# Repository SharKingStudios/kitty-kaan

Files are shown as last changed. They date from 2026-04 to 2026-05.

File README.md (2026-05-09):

# kitty kaan

*Acceleration controlled cat ears for our FRC driver ;)*

## What is this?

**kitty kaan** is a wearable pair of motorized cat ears designed for our FRC driver. The ears react to acceleration, making them move with the driver in a more expressive way.

The project combines a small electronics stack and compact mounting hardware into a lightweight assembly. An accelerometer detects motion, and the control electronics translate that movement into ear movement. The result is a simple but very silly accessory that gives the driver a pair of responsive “kitty ears.”

This was designed as a small CAD and electronics integration project. A big part of the challenge was packaging everything into the smallest form factor possible while still keeping the assembly buildable. Instead of using one large controller board, the electronics were split across smaller breakout boards so they could fit into tighter spaces and be arranged more flexibly.

---

## Renders

Screenshot 2026-04-08 at 22-41-47 Kitty Kaan Main Assembly




---

## Some context

Its a simpler project for a simple idea.

The goal was to make the electronics stack as small as physically possible, which is why seperate breakouts were used. They also added to the simplicity of the design (which is nice).

Fitting everything together was the hardest part of this mini project, but it turned out looking pretty awesome!

## Journaling

This project was made for Hack Club's Stasis program!

You can check out my project journal [here](https://stasis.hackclub.com/dashboard/projects/cmni7bl1i00i401np7ca4izak)!

## Bill of Materials

| Qty | Item | URL | Unit Price (USD) | Total (USD) | Notes |
| ---: | --- | --- | ---: | ---: | --- |
| 1 | Adafruit MiniBoost 5V @ 1A - TPS61023 | [adafruit.com/product/4654](https://www.adafruit.com/product/4654) | $3.95 | $3.95 |  |
| 1 | 9g Servo Set | [Amazon](https://www.amazon.com/Control-Raspberry-Helicopter-Airplane-Controls/dp/B0DFL7QZRJ) | $6.99 | $6.99 | For 4× 9g servos |
| 1 | Seeed XIAO RA4M1 | [Amazon](https://www.amazon.com/Compatible-Arduino-Renesas-Tolerant-Ultra-Compact/dp/B0DF9VJDJ7) | $9.90 | $9.90 |  |
| 1 | JST Battery Connector | — | $0.00 | $0.00 | Whatever matches your battery |
| 1 | Some Battery | — | $0.00 | $0.00 | Pick your favorite |
| 1 | MPU-6050 IMU | [Amazon](https://www.amazon.com/HiLetgo-MPU-6050-Accelerometer-Gyroscope-Converter/dp/B01DK83ZYQ) | $6.99 | $6.99 |  |
| 1 | PCB + Shipping | JLCPCB | $15.00 | $15.00 |  |
|  | **Total** |  |  | **$42.83** |  |

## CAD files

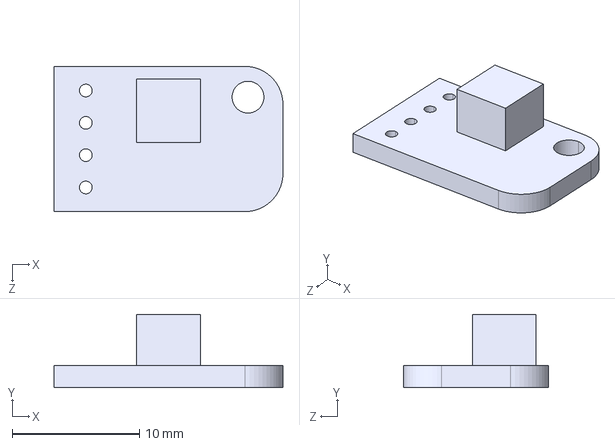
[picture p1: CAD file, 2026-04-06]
PCB/Custom Parts/Adafruit TPS61023.STEP
18.0 x 5.75 x 11.4 mm

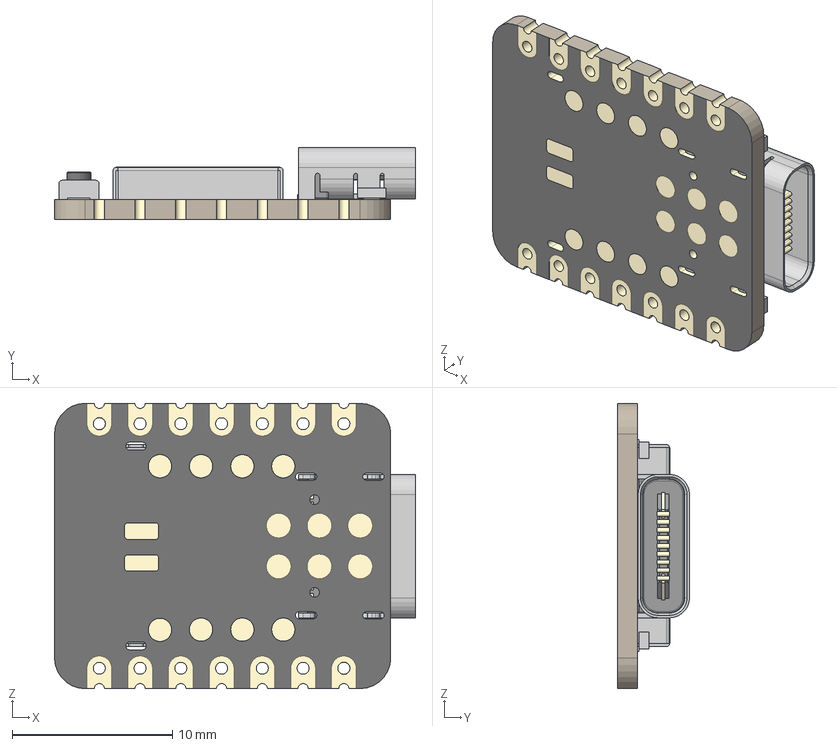
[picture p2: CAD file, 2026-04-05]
PCB/Custom Parts/Seeed Studio XIAO RA4M1 v3.step
22.5 x 4.49 x 17.8 mm
BOSS-EXTRUDE14_8_
BOSS-EXTRUDE7_4_
BOSS-EXTRUDE7_3_
BOSS-EXTRUDE14_4_
BOSS-EXTRUDE14_2_
BOSS-EXTRUDE14_11_
BOSS-EXTRUDE7_7_
BOSS-EXTRUDE14_9_
BOSS-EXTRUDE14_3_
BOSS-EXTRUDE14_7_
MIRROR2
BOSS-EXTRUDE14_5_
BOSS-EXTRUDE14_12_
BOSS-EXTRUDE7_8_
BOSS-EXTRUDE7_1_
BOSS-EXTRUDE14_10_
BOSS-EXTRUDE7_9_
BOSS-EXTRUDE14_6_
BOSS-EXTRUDE14_1_
BOSS-EXTRUDE7_6_
BOSS-EXTRUDE7_2_
CUT-EXTRUDE5
BOSS-EXTRUDE7_5_
Button (1) x 2
Shield

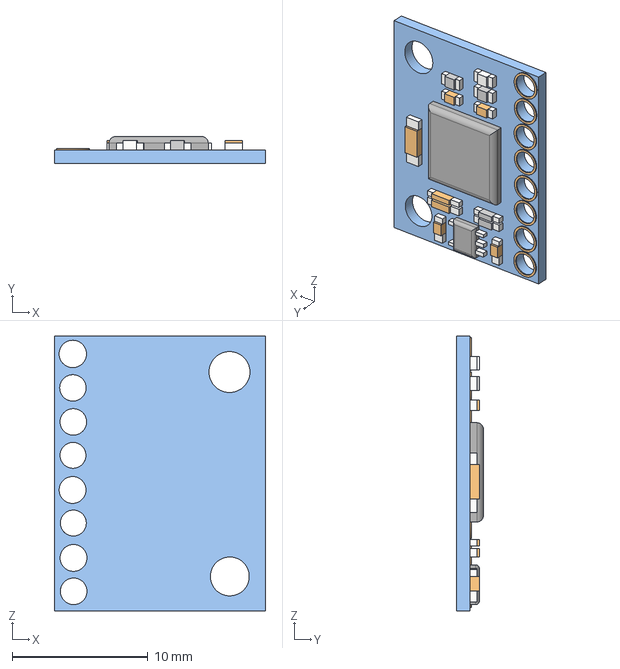
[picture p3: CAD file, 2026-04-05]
PCB/Custom Parts/MPU6050 v2.step
15.6 x 2.00 x 20.3 mm

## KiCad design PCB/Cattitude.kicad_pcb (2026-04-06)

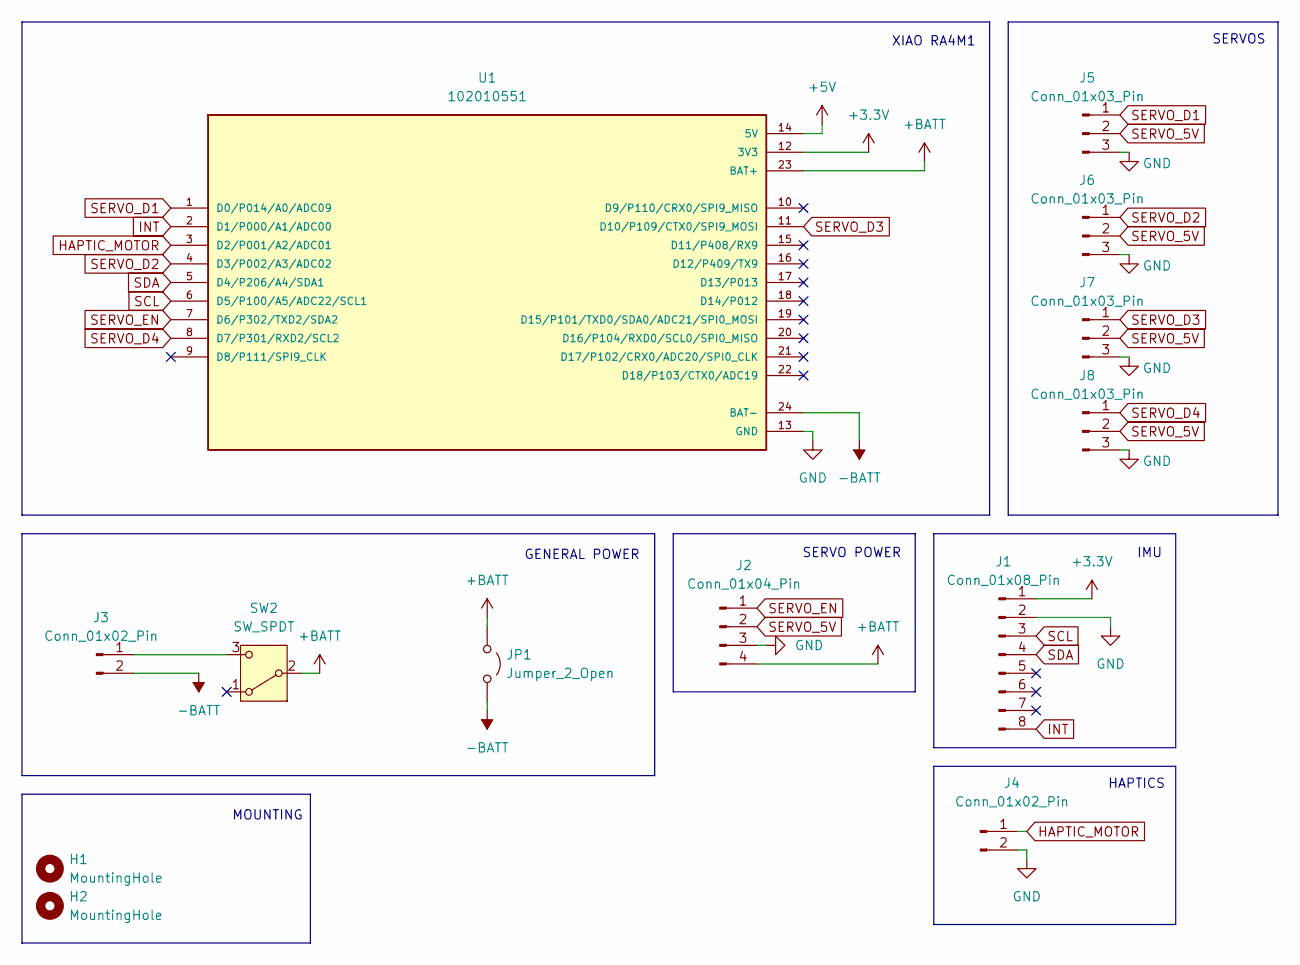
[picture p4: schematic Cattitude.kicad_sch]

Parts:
H1, H2: MountingHole; MountingHole_2.7mm_M2.5_DIN965_Pad
J1: Conn_01x08_Pin; MPU 6050
J2: Conn_01x04_Pin; PinHeader_1x04_P2.54mm_Vertical
J3: Conn_01x02_Pin; JST_EH_B2B-EH-A_1x02_P2.50mm_Vertical
J4: Conn_01x02_Pin; PinHeader_1x02_P2.54mm_Vertical
J5, J6, J7, J8: Conn_01x03_Pin; PinHeader_1x03_P2.54mm_Horizontal
JP1: Jumper_2_Open; TestPoint_2Pads_Pitch2.54mm_Drill0.8mm
SW2: SW_SPDT; SW_Slide_SPDT_Angled_CK_OS102011MA1Q
U1: 102010551; XIAO RA4M1; PARTREV NA

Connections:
+3.3V: J1.1, U1.12 (3V3)
+5V: U1.14 (5V)
+BATT: J2.4, JP1.1 (A), SW2.2 (B), U1.23 (BAT+)
-BATT: J3.2, JP1.2 (B), U1.24 (BAT-)
GND: J1.2, J2.3, J4.2, J5.3, J6.3, J7.3, J8.3, U1.13 (GND)
HAPTIC_MOTOR: J4.1, U1.3 (D2/P001/A2/ADC01)
INT: J1.8, U1.2 (D1/P000/A1/ADC00)
unnamed: J3.1, SW2.3 (C)
SCL: J1.3, U1.6 (D5/P100/A5/ADC22/SCL1)
SDA: J1.4, U1.5 (D4/P206/A4/SDA1)
SERVO_5V: J2.2, J5.2, J6.2, J7.2, J8.2
SERVO_D1: J5.1, U1.1 (D0/P014/A0/ADC09)
SERVO_D2: J6.1, U1.4 (D3/P002/A3/ADC02)
SERVO_D3: J7.1, U1.11 (D10/P109/CTX0/SPI9_MOSI)
SERVO_D4: J8.1, U1.8 (D7/P301/RXD2/SCL2)
SERVO_EN: J2.1, U1.7 (D6/P302/TXD2/SDA2)

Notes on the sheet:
SERVOS
MOUNTING
HAPTICS
XIAO RA4M1
SERVO POWER
GENERAL POWER
IMU

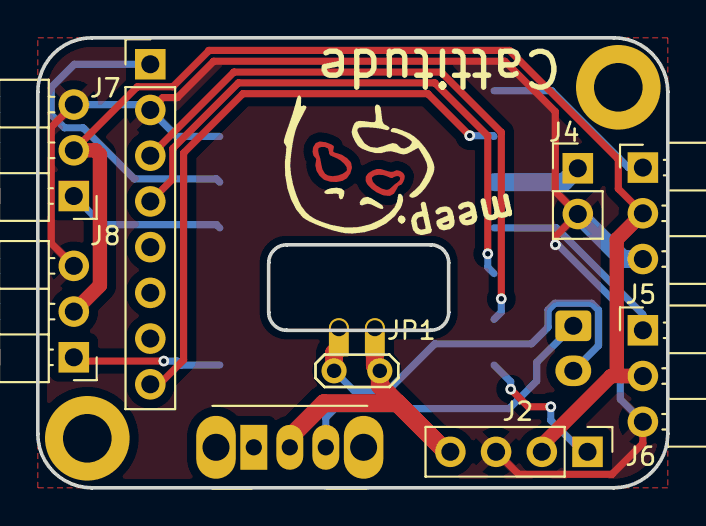
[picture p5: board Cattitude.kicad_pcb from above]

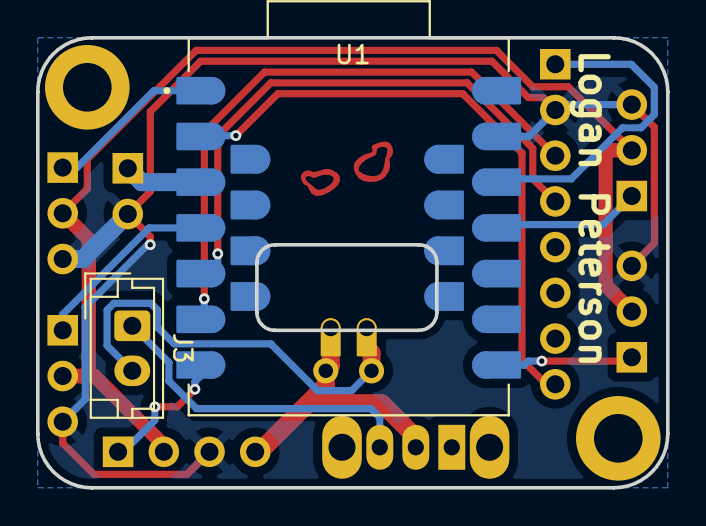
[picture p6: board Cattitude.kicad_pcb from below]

Board: 2 copper layers, 35.0 x 25.0 mm, 13 parts (2 on the bottom side), 15 nets.

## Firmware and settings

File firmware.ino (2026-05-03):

/*
  Kitty Kaan Cat Ear Firmware
  Board: Seeed XIAO RA4M1
  IMU: MPU6050/GY-521 style module
  Servos: 4 expressive cat-ear servos

  Schematic pin mapping:
    SERVO_D1  -> D0
    IMU_INT   -> D1
    HAPTIC    -> D2, unused here
    SERVO_D2  -> D3
    SDA       -> D4
    SCL       -> D5
    SERVO_EN  -> D6
    SERVO_D4  -> D7
    SERVO_D3  -> D10
*/

#include <Wire.h>
#include <Servo.h>
#include <Adafruit_MPU6050.h>
#include <Adafruit_Sensor.h>

#if defined(ARDUINO_ARCH_RENESAS)
  #include <Arduino.h>
#endif

// -------------------- Pins --------------------

const int PIN_SERVO_1 = D0;
const int PIN_IMU_INT = D1;
const int PIN_HAPTIC  = D2;
const int PIN_SERVO_2 = D3;
const int PIN_SERVO_EN = D6;
const int PIN_SERVO_4 = D7;
const int PIN_SERVO_3 = D10;

const int PIN_STATUS_LED = LED_BUILTIN;

// Battery ADC pin.
// If your XIAO core exposes PIN_VBAT or BATTERY_PIN, this will use it.
// If not, battery monitoring will safely default to 100%.
#if defined(PIN_VBAT)
const int PIN_BATTERY_ADC = PIN_VBAT;
#elif defined(BATTERY_PIN)
const int PIN_BATTERY_ADC = BATTERY_PIN;
#elif defined(VBAT_ENABLE)
const int PIN_BATTERY_ADC = VBAT_ENABLE;
#else
const int PIN_BATTERY_ADC = -1;
#endif

// -------------------- Hardware --------------------

Adafruit_MPU6050 mpu;

Servo servo1;
Servo servo2;
Servo servo3;
Servo servo4;

volatile bool imuInterruptSeen = false;

// -------------------- Tuning --------------------

// Servo center positions.
// Adjust these if your mechanical center is not exactly 90.
int center1 = 90;
int center2 = 90;
int center3 = 90;
int center4 = 90;

// Servo travel limits.
const int SERVO_MIN = 35;
const int SERVO_MAX = 145;

// Overall expressiveness.
const float PITCH_GAIN = 0.95f;
const float ROLL_GAIN  = 0.80f;
const float SWAY_GAIN  = 1.15f;

// Smoothness.
// Higher = smoother/slower.
const float SERVO_SMOOTHING = 0.13f;

// Movement thresholds.
const float ACTIVE_ACCEL_DELTA_G = 0.065f;
const float ACTIVE_GYRO_DPS      = 4.0f;

// Sleep after this much stillness.
const unsigned long SLEEP_AFTER_MS = 90000UL;

// Low battery cutoff.
const float LOW_BATTERY_PERCENT = 20.0f;

// LiPo voltage range.
const float LIPO_EMPTY_V = 3.30f;
const float LIPO_FULL_V  = 4.20f;

// If your battery ADC reads through a divider, set this.
// Example: 2.0 if ADC sees half the battery voltage.
// For built-in VBAT sensing this is often already handled by the core,
// but leave this here for easy adjustment.
const float BATTERY_DIVIDER_RATIO = 1.0f;

// XIAO / Arduino ADC reference assumption.
// Adjust only if your board core reports a different ADC scale.
const float ADC_REFERENCE_V = 3.3f;
const int ADC_MAX_COUNTS = 4095;

// Servo update rate.
const unsigned long SERVO_UPDATE_MS = 20;

// -------------------- State --------------------

float servoPos1 = 90;
float servoPos2 = 90;
float servoPos3 = 90;
float servoPos4 = 90;

float sway = 0.0f;
float swayVelocity = 0.0f;

unsigned long lastMotionMs = 0;
unsigned long lastServoUpdateMs = 0;
unsigned long lastBatteryCheckMs = 0;
unsigned long lastLowBatteryBlinkMs = 0;

float batteryPercent = 100.0f;
bool lowBattery = false;
bool servosEnabled = false;

// -------------------- Helpers --------------------

void imuISR() {
  imuInterruptSeen = true;
}

int clampServo(int v) {
  if (v < SERVO_MIN) return SERVO_MIN;
  if (v > SERVO_MAX) return SERVO_MAX;
  return v;
}

float clampFloat(float v, float lo, float hi) {
  if (v < lo) return lo;
  if (v > hi) return hi;
  return v;
}

float lipoVoltageToPercent(float v) {
  // Simple single-cell LiPo percentage curve.
  // This is intentionally conservative around the lower end.
  if (v >= 4.20f) return 100.0f;
  if (v <= 3.30f) return 0.0f;

  if (v >= 4.10f) return 90.0f + (v - 4.10f) * 100.0f;
  if (v >= 4.00f) return 75.0f + (v - 4.00f) * 150.0f;
  if (v >= 3.90f) return 55.0f + (v - 3.90f) * 200.0f;
  if (v >= 3.80f) return 35.0f + (v - 3.80f) * 200.0f;
  if (v >= 3.70f) return 20.0f + (v - 3.70f) * 150.0f;
  if (v >= 3.60f) return 10.0f + (v - 3.60f) * 100.0f;
  return (v - 3.30f) * 33.33f;
}

float readBatteryVoltage() {
  if (PIN_BATTERY_ADC < 0) {
    return 4.20f;
  }

  analogReadResolution(12);

  const int samples = 16;
  long total = 0;

  for (int i = 0; i < samples; i++) {
    total += analogRead(PIN_BATTERY_ADC);
    delay(2);
  }

  float raw = total / float(samples);
  float measured = (raw / ADC_MAX_COUNTS) * ADC_REFERENCE_V;
  return measured * BATTERY_DIVIDER_RATIO;
}

void updateBatteryStatus() {
  unsigned long now = millis();

  if (now - lastBatteryCheckMs < 5000UL) {
    return;
  }

  lastBatteryCheckMs = now;

  float vbat = readBatteryVoltage();
  batteryPercent = lipoVoltageToPercent(vbat);
  lowBattery = batteryPercent < LOW_BATTERY_PERCENT;
}

void enableServos() {
  if (servosEnabled) return;

  digitalWrite(PIN_SERVO_EN, HIGH);
  delay(100);

  servo1.attach(PIN_SERVO_1);
  servo2.attach(PIN_SERVO_2);
  servo3.attach(PIN_SERVO_3);
  servo4.attach(PIN_SERVO_4);

  servosEnabled = true;
}

void disableServos() {
  if (!servosEnabled) return;

  servo1.detach();
  servo2.detach();
  servo3.detach();
  servo4.detach();

  delay(20);
  digitalWrite(PIN_SERVO_EN, LOW);

  servosEnabled = false;
}

void writeServoSmooth(Servo &s, float &current, int target) {
  current += (target - current) * SERVO_SMOOTHING;
  s.write(clampServo((int)(current + 0.5f)));
}

void centerEarsAndStop() {
  enableServos();

  for (int i = 0; i < 60; i++) {
    writeServoSmooth(servo1, servoPos1, center1);
    writeServoSmooth(servo2, servoPos2, center2);
    writeServoSmooth(servo3, servoPos3, center3);
    writeServoSmooth(servo4, servoPos4, center4);
    delay(20);
  }

  disableServos();
}

void blinkLowBattery() {
  unsigned long now = millis();

  if (now - lastLowBatteryBlinkMs >= 500UL) {
    lastLowBatteryBlinkMs = now;
    digitalWrite(PIN_STATUS_LED, !digitalRead(PIN_STATUS_LED));
  }
}

void configureMPUMotionInterrupt() {
  // Motion interrupt is used to wake from idle/light sleep.
  // Threshold is in MPU6050 motion units, not g directly.
  mpu.setHighPassFilter(MPU6050_HIGHPASS_0_63_HZ);
  mpu.setMotionDetectionThreshold(3);
  mpu.setMotionDetectionDuration(20);
  mpu.setInterruptPinLatch(true);
  mpu.setInterruptPinPolarity(true);
  mpu.setMotionInterrupt(true);
}

void clearMPUInterrupt() {
  sensors_event_t a, g, temp;
  mpu.getEvent(&a, &g, &temp);
  imuInterruptSeen = false;
}

void enterLightSleepUntilMotion() {
  centerEarsAndStop();

  clearMPUInterrupt();
  attachInterrupt(digitalPinToInterrupt(PIN_IMU_INT), imuISR, RISING);

  digitalWrite(PIN_STATUS_LED, LOW);

  while (!imuInterruptSeen) {
    updateBatteryStatus();

    if (lowBattery) {
      blinkLowBattery();
      delay(100);
      continue;
    }

    // ARM light sleep. An external interrupt wakes execution here.
    #if defined(__arm__) || defined(ARDUINO_ARCH_RENESAS)
      __DSB();
      __WFI();
      __ISB();
    #else
      delay(250);
    #endif
  }

  detachInterrupt(digitalPinToInterrupt(PIN_IMU_INT));
  clearMPUInterrupt();

  lastMotionMs = millis();
  digitalWrite(PIN_STATUS_LED, HIGH);
}

// -------------------- Setup --------------------

void setup() {
  pinMode(PIN_SERVO_EN, OUTPUT);
  digitalWrite(PIN_SERVO_EN, LOW);

  pinMode(PIN_STATUS_LED, OUTPUT);
  digitalWrite(PIN_STATUS_LED, HIGH);

  pinMode(PIN_HAPTIC, OUTPUT);
  digitalWrite(PIN_HAPTIC, LOW);

  pinMode(PIN_IMU_INT, INPUT);

  Wire.begin();

  if (!mpu.begin()) {
    // IMU failed. Blink fast forever.
    while (1) {
      digitalWrite(PIN_STATUS_LED, !digitalRead(PIN_STATUS_LED));
      delay(120);
    }
  }

  // IMU tuning.
  mpu.setAccelerometerRange(MPU6050_RANGE_4_G);
  mpu.setGyroRange(MPU6050_RANGE_500_DEG);
  mpu.setFilterBandwidth(MPU6050_BAND_21_HZ);

  configureMPUMotionInterrupt();

  enableServos();

  servo1.write(center1);
  servo2.write(center2);
  servo3.write(center3);
  servo4.write(center4);

  servoPos1 = center1;
  servoPos2 = center2;
  servoPos3 = center3;
  servoPos4 = center4;

  lastMotionMs = millis();
}

// -------------------- Main Loop --------------------

void loop() {
  updateBatteryStatus();

  if (lowBattery) {
    centerEarsAndStop();

    while (true) {
      updateBatteryStatus();
      blinkLowBattery();

      if (!lowBattery) {
        enableServos();
        lastMotionMs = millis();
        break;
      }

      delay(100);
    }
  }

  unsigned long now = millis();

  if (now - lastServoUpdateMs < SERVO_UPDATE_MS) {
    return;
  }

  lastServoUpdateMs = now;

  sensors_event_t accel, gyro, temp;
  mpu.getEvent(&accel, &gyro, &temp);

  float ax = accel.acceleration.x / 9.80665f;
  float ay = accel.acceleration.y / 9.80665f;
  float az = accel.acceleration.z / 9.80665f;

  float gx = gyro.gyro.x * 57.2958f;
  float gy = gyro.gyro.y * 57.2958f;
  float gz = gyro.gyro.z * 57.2958f;

  float accelMag = sqrt(ax * ax + ay * ay + az * az);
  float accelDelta = fabs(accelMag - 1.0f);
  float gyroMag = sqrt(gx * gx + gy * gy + gz * gz);

  bool moving = accelDelta > ACTIVE_ACCEL_DELTA_G || gyroMag > ACTIVE_GYRO_DPS;

  if (moving) {
    lastMotionMs = now;
  }

  if (now - lastMotionMs > SLEEP_AFTER_MS) {
    enterLightSleepUntilMotion();
    return;
  }

  enableServos();

  // Estimate head tilt.
  float pitchDeg = atan2(-ax, sqrt(ay * ay + az * az)) * 57.2958f;
  float rollDeg  = atan2(ay, az) * 57.2958f;

  pitchDeg = clampFloat(pitchDeg, -35.0f, 35.0f);
  rollDeg  = clampFloat(rollDeg, -35.0f, 35.0f);

  // Springy sway from head motion.
  // Gyro Z gives a nice side-to-side laggy ear motion.
  float swayForce = gz * 0.018f;
  swayVelocity += swayForce;
  swayVelocity *= 0.88f;
  sway += swayVelocity;
  sway *= 0.92f;

  sway = clampFloat(sway, -28.0f, 28.0f);

  float pitchMove = pitchDeg * PITCH_GAIN;
  float rollMove  = rollDeg  * ROLL_GAIN;
  float swayMove  = sway     * SWAY_GAIN;

  // Four-servo expressive mapping.
  //
  // Assumption:
  //   servo1/servo2 = one ear pair
  //   servo3/servo4 = other ear pair
  //
  // If an ear moves backwards from what you want,
  // flip the sign for that servo below.
  int target1 = center1 + pitchMove + rollMove + swayMove;
  int target2 = center2 - pitchMove + rollMove + swayMove * 0.65f;
  int target3 = center3 + pitchMove - rollMove - swayMove;
  int target4 = center4 - pitchMove - rollMove - swayMove * 0.65f;

  target1 = clampServo(target1);
  target2 = clampServo(target2);
  target3 = clampServo(target3);
  target4 = clampServo(target4);

  writeServoSmooth(servo1, servoPos1, target1);
  writeServoSmooth(servo2, servoPos2, target2);
  writeServoSmooth(servo3, servoPos3, target3);
  writeServoSmooth(servo4, servoPos4, target4);
}

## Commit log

2026-04-05 Imported Parts + Finished Schematic
    [Cattitude.kicad_pcb, Cattitude.kicad_sch, MPU6050 v2.step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]
2026-04-06 PCB Routing done
    [Adafruit TPS61023.STEP, Cattitude.kicad_pcb, Cattitude.kicad_sch]
2026-04-06 Board Cleanup + Production Files
    [Cattitude-B_Cu.gbr, Cattitude-B_Mask.gbr, Cattitude-B_Paste.gbr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]
2026-04-06 Added GND Pour
    [Cattitude-B_Cu.gbr, Cattitude-B_Mask.gbr, Cattitude-B_Paste.gbr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]
2026-04-09 Add Bill of Materials (BOM) CSV file
    [BOM.csv]
2026-04-09 Add CAD Assembly
2026-04-09 Revise BOM.csv with corrected prices and entries
    Updated prices and formatting for BOM items.
    [BOM.csv]
2026-05-03 Add initial firmware for Kitty Kaan Cat Ear
    Initial commit of firmware for Kitty Kaan Cat Ear project, including setup for IMU and servo control.
2026-05-09 Update README with project details and BOM
    Added project description and Bill of Materials to README.
